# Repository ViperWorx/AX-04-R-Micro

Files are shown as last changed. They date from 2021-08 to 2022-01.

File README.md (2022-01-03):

<h1>AX-04-R Micro Core XY 3D Printer</h1>
<h3>Small, Compact, Rapid 3D Printer.</h3>

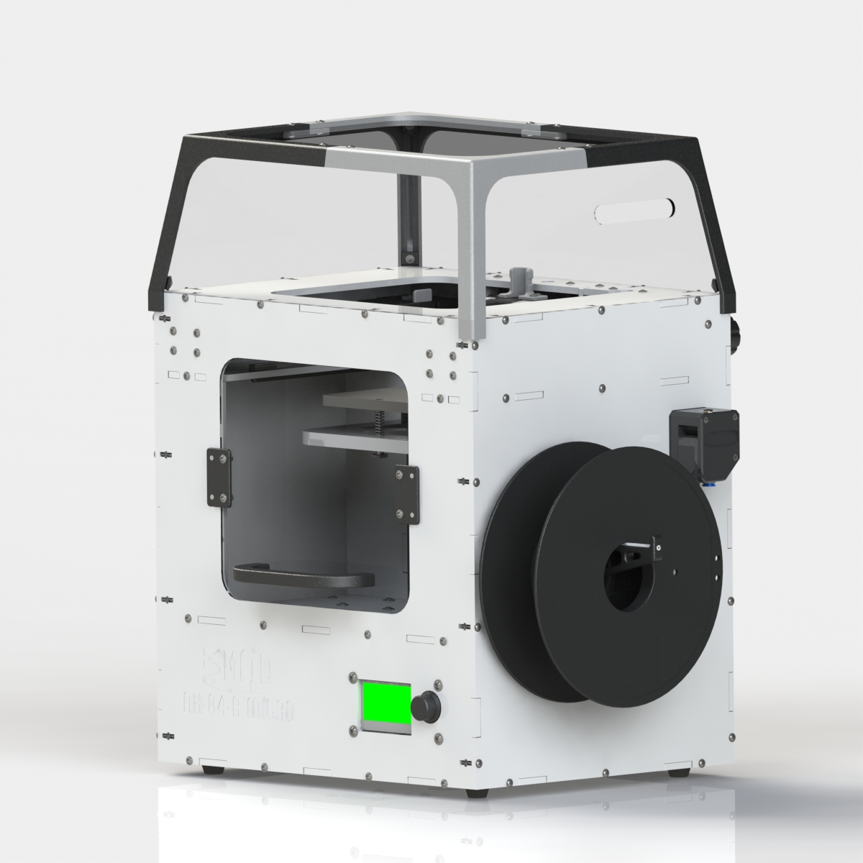
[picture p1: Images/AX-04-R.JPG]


The AX-04-R is a Acrylic bodied 3D Printer with a 120mm³ build volume.

<h4>Bill of Materials</h4>
You can find the Bill of material <a href="https://docs.google.com/spreadsheets/d/1N3T2BKN8lVm5PpJpeCxoxXIL51K7zTlElqo2wkVUTho/edit?usp=sharing">here</a>

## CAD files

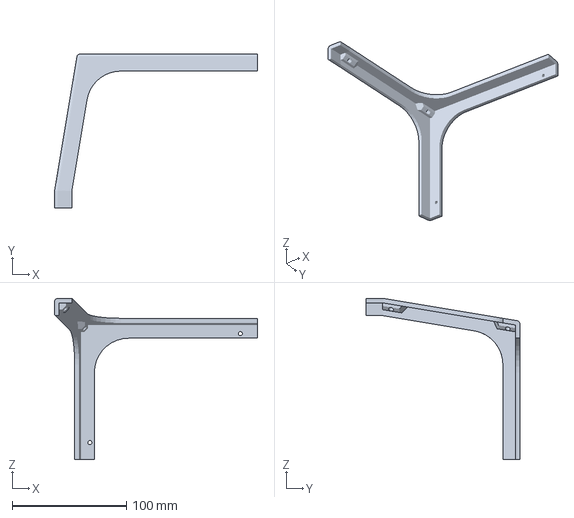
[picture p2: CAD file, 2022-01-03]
3MF/Top Hat Frame Quarter 2.3MF
178.0 x 135.0 x 141.5 mm

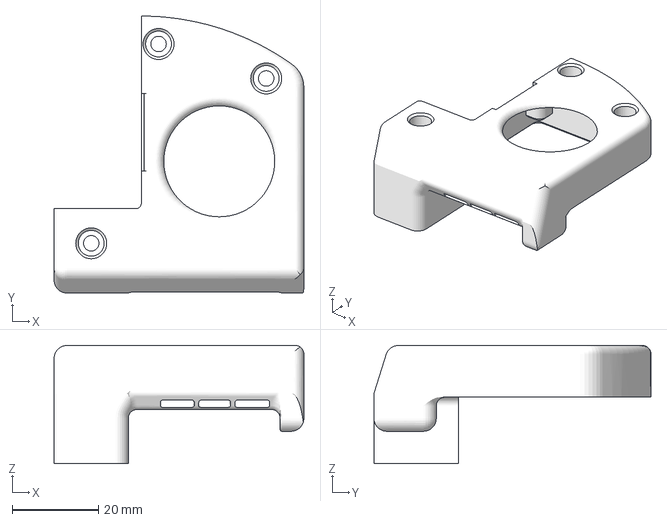
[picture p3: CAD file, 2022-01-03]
3MF/Layer Fan Mount Left.3MF
58.0 x 64.3 x 27.4 mm

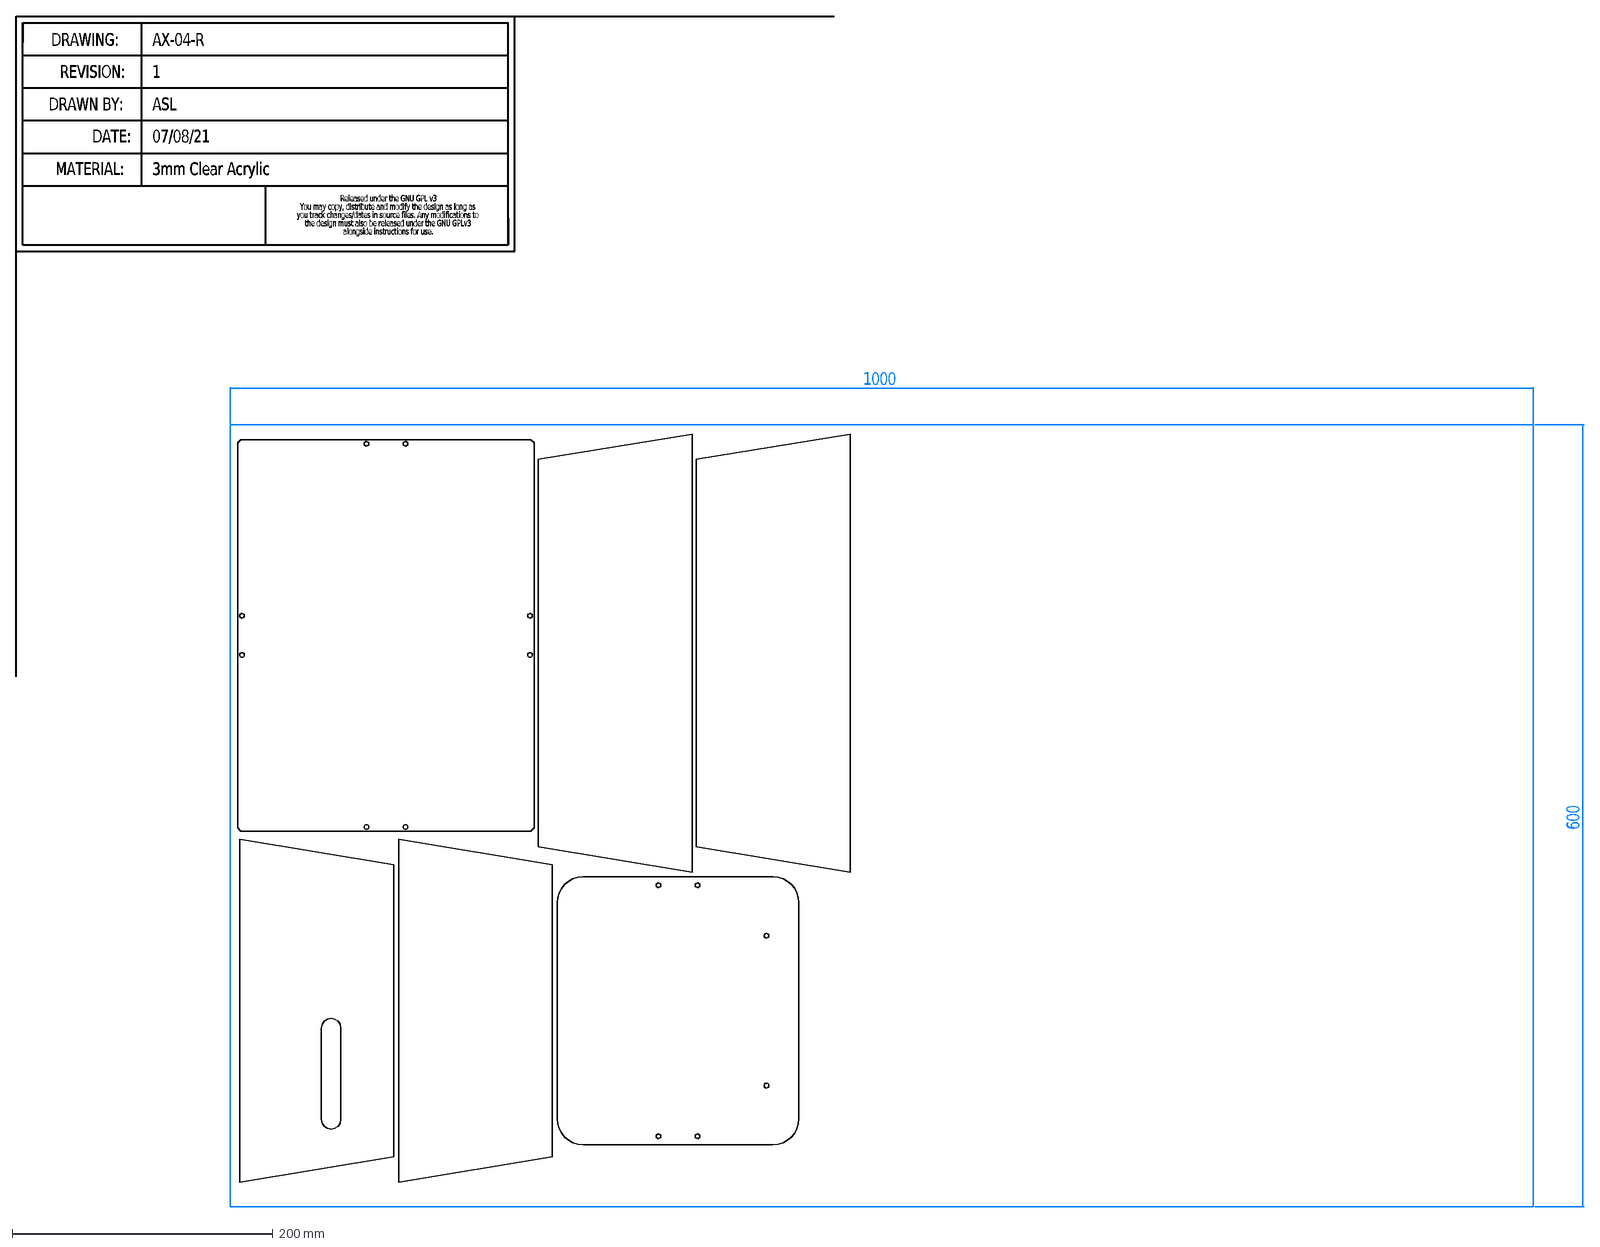
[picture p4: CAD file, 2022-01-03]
DXF/AX-04-R 3mm Clear Acrylic Laser Cut Parts.DXF
1000
600
Released under the GNU GPL v3
You may copy, distribute and modify the design as long as
you track changes/dates in source files. Any modifications to
the design must also be released under the GNU GPLv3
alongside instructions for use.
DRAWING:
REVISION:
DRAWN BY:
DATE:
MATERIAL:
AX-04-R
1
ASL
07/08/21
3mm Clear Acrylic

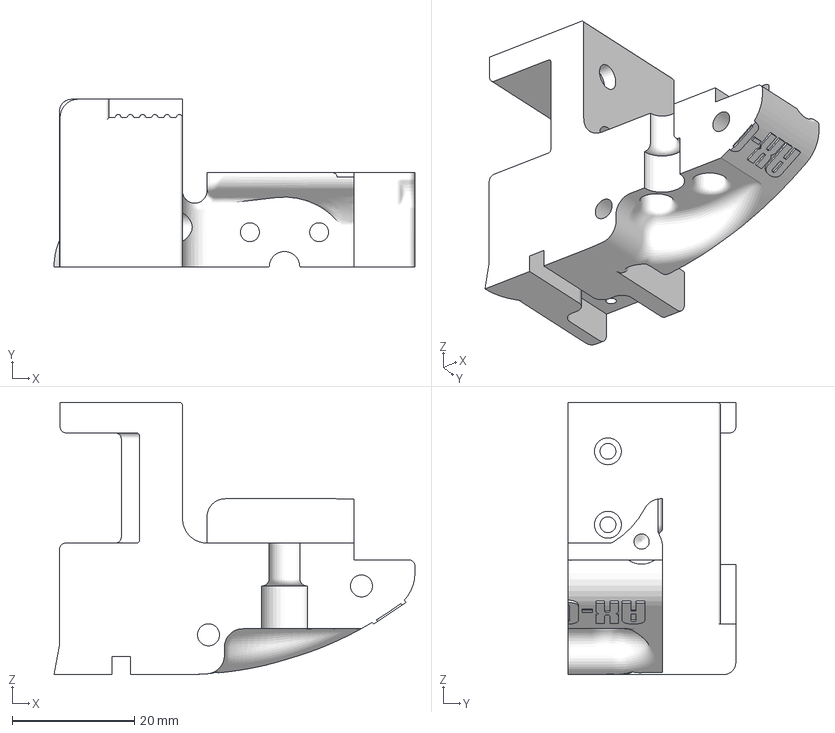
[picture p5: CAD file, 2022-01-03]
3MF/X Mount Left -Dragon Hotend.3MF
59.0 x 27.4 x 44.5 mm

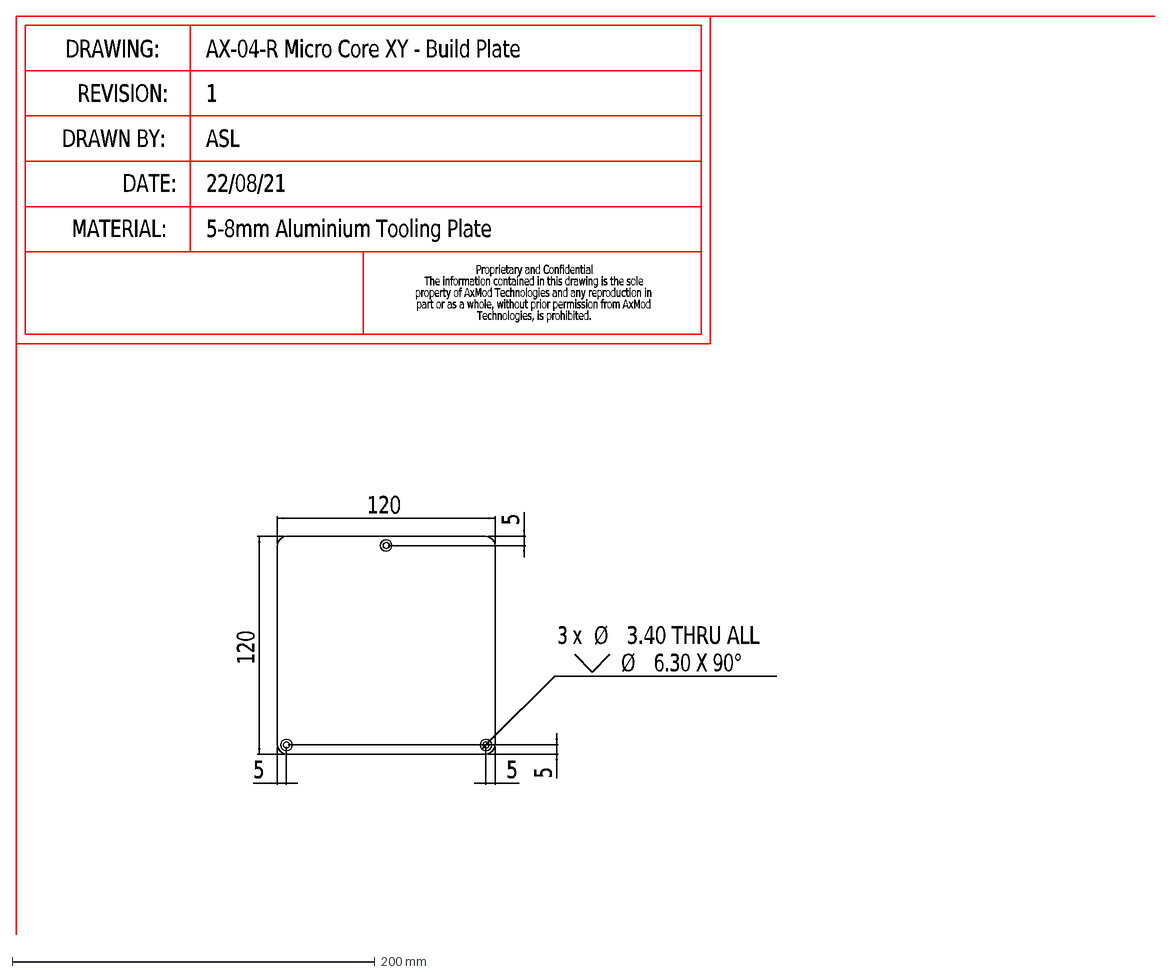
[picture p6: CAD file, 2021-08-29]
DXF/120x120 Print Bed.DXF
Proprietary and Confidential
The information contained in this drawing is the sole
property of AxMod Technologies and any reproduction in
part or as a whole, without prior permission from AxMod
Technologies, is prohibited.
DRAWING:
REVISION:
DRAWN BY:
DATE:
MATERIAL:
AX-04-R Micro Core XY - Build Plate
1
ASL
22/08/21
5-8mm Aluminium Tooling Plate
120
5
3 x
Ø
3.40 THRU ALL
6.30 X 90°

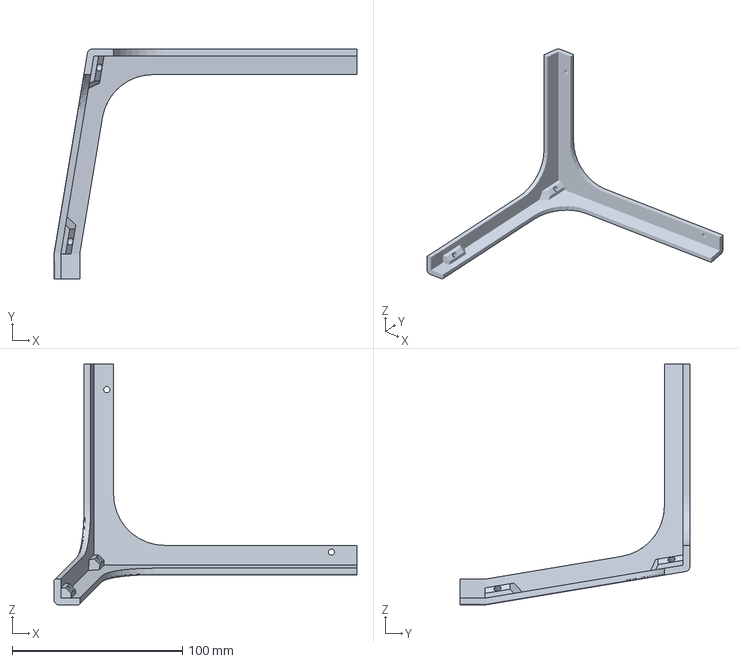
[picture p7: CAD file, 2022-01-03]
3MF/Top Hat Frame Quarter 4.3MF
178.0 x 135.0 x 141.5 mm

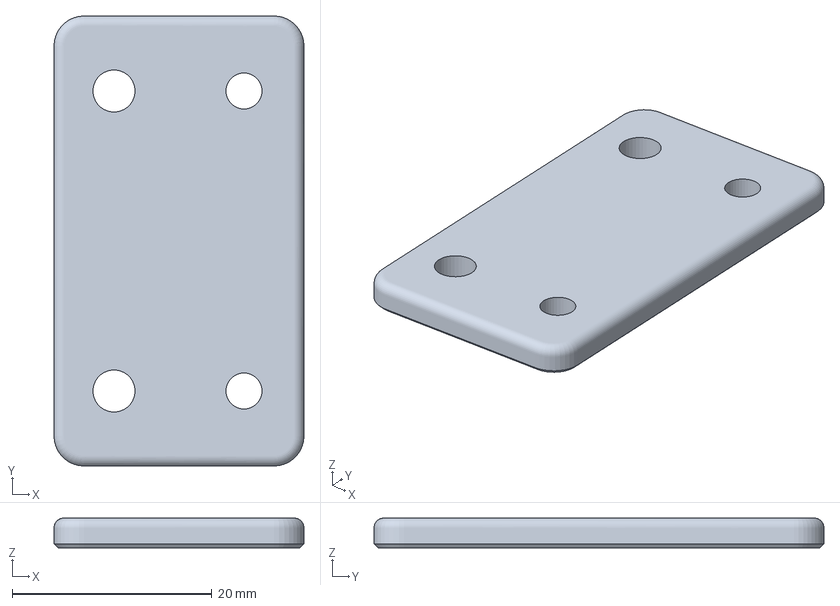
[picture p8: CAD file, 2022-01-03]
3MF/Front Window Magnet Plate.3MF
25.0 x 45.0 x 3.00 mm

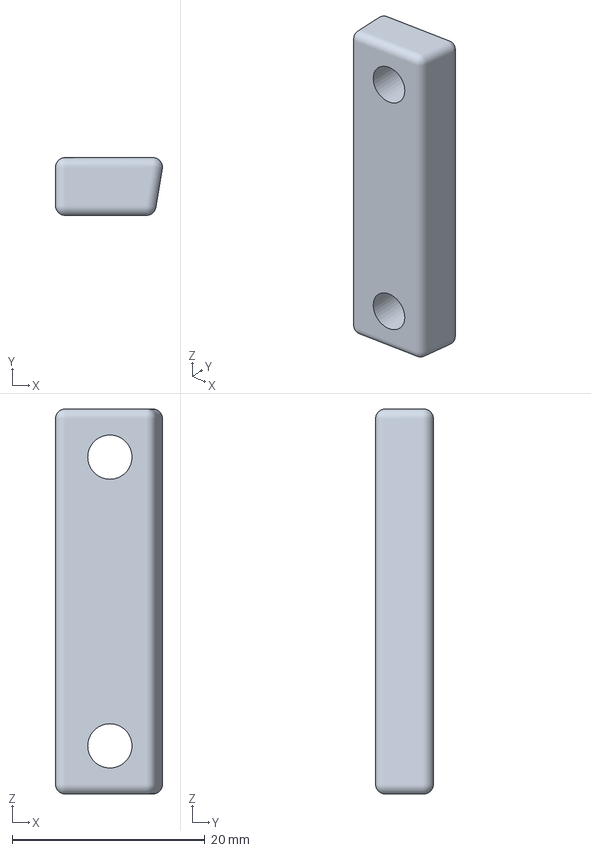
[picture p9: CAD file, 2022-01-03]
3MF/Top Hat Window Retainer Block Top.3MF
11.1 x 6.00 x 40.0 mm

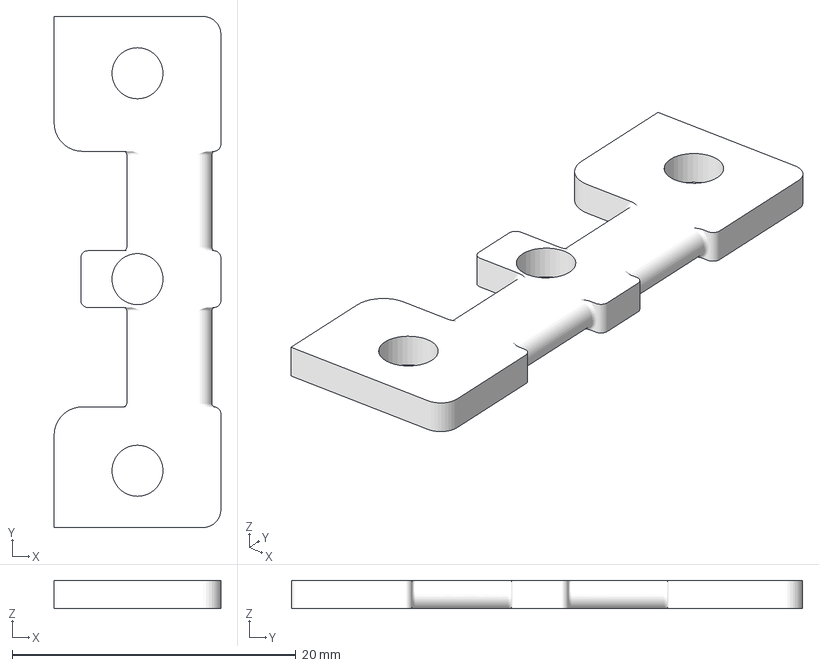
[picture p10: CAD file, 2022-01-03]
3MF/XY Belt Clamp.3MF
11.8 x 36.0 x 2.00 mm

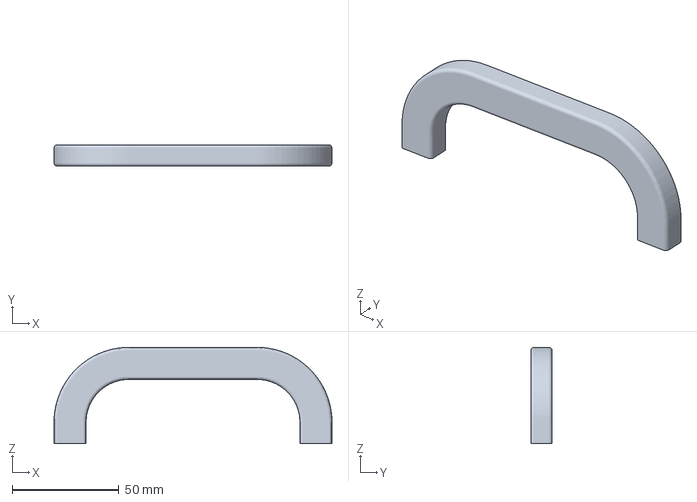
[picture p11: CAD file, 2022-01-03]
3MF/Front Window Handle.3MF
130.0 x 10.0 x 45.0 mm

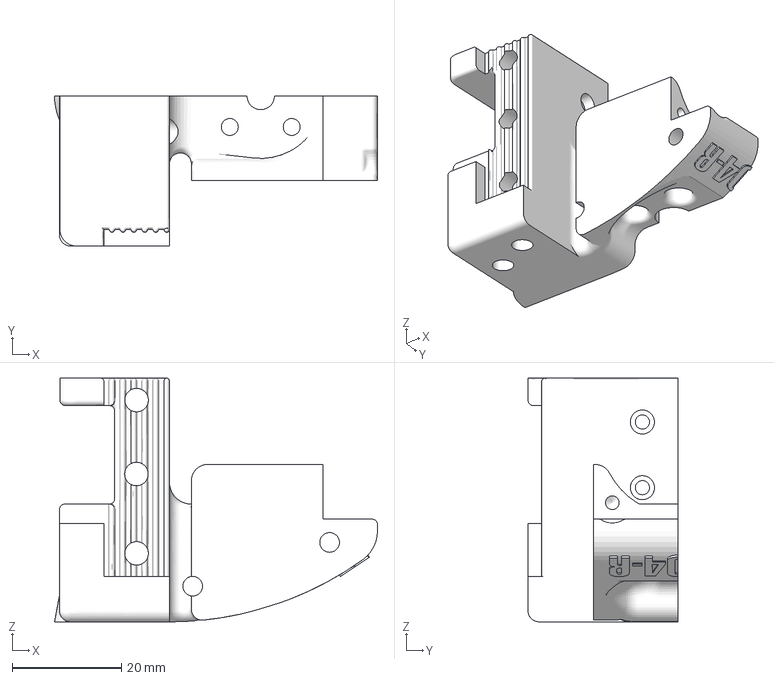
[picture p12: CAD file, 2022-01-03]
3MF/X Mount Right - Dragon Hotend.3MF
59.0 x 27.4 x 44.5 mm

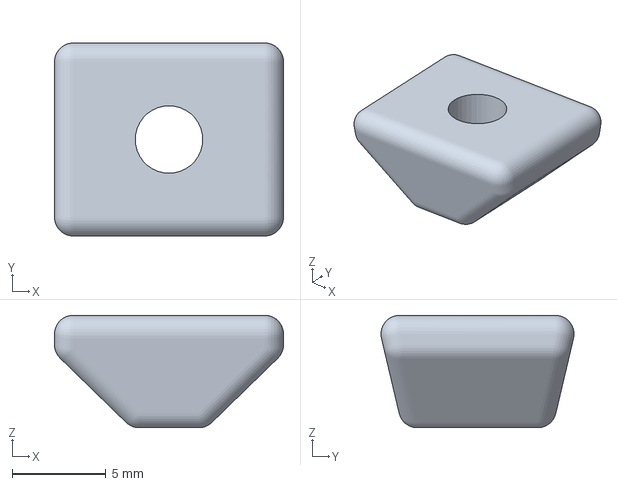
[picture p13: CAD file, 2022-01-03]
3MF/Top Hat Window Retainer Block Side.3MF
12.2 x 10.3 x 6.00 mm

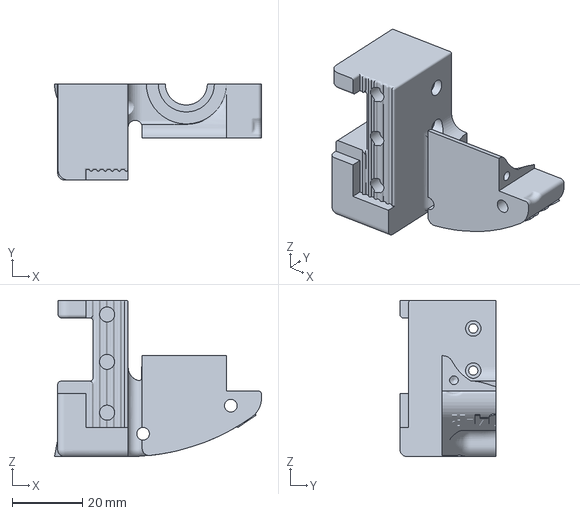
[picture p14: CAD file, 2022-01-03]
3MF/X Mount Right - Groovemount (E3D v6).3MF
59.0 x 27.4 x 44.5 mm

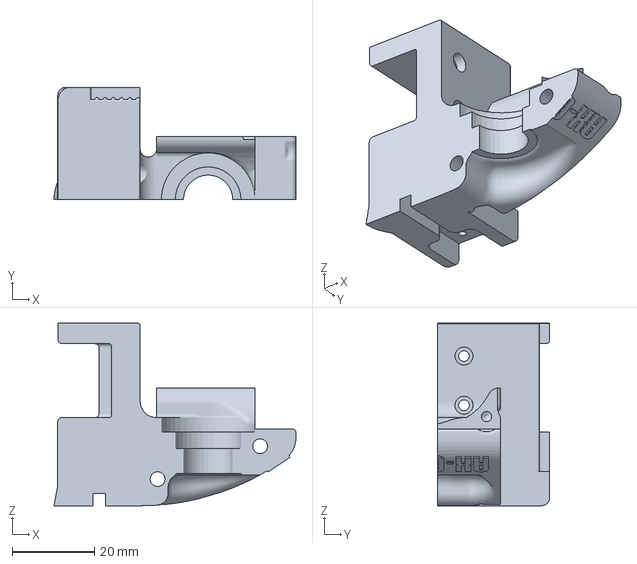
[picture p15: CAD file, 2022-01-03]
3MF/X Mount Left - Groovemount (E3D v6).3MF
59.0 x 27.4 x 44.5 mm

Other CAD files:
DXF/AX-04-R 5mm Acrylic Laser Cut Parts.DXF
3MF/Layer Fan Mount Right.3MF
3MF/Top Hat Frame Quarter 3.3MF
3MF/Top Hat Frame Quarter 1.3MF
3MF/Extruder Motor Shim.3MF
3MF/Foot Base.3MF
3MF/Idler Spacer.3MF
3MF/LED Mount Left-Right.3MF
3MF/LED Mount Top.3MF
3MF/M3 Stand off.3MF
3MF/Rail Retaining Bar - Half.3MF
3MF/Rail Retaining Bar.3MF
3MF/Spool Hanger.3MF
3MF/Tensioning Knob.3MF
3MF/X Alignment Tool.3MF
3MF/X Axis Umbilical Strain Relief Tool Head.3MF
3MF/X Axis Umbilical Strain Relief.3MF
3MF/X Endstop Interface.3MF
3MF/XY Idler Front Bottom Half.3MF
3MF/XY Idler Front Top Half.3MF
3MF/XY Motor Cap Left.3MF
3MF/XY Motor Cap Right.3MF
3MF/XY Motor Mount Left Bottom.3MF
3MF/XY Motor Mount Right Bottom.3MF
3MF/Y Carriage Left Bottom.3MF
3MF/Y Carriage Left Top.3MF
3MF/Y Carriage Right Bottom.3MF
3MF/Y Carriage Right Top.3MF
3MF/Y Endstop Mount.3MF
3MF/YZ Rail Alignment Tool.3MF
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

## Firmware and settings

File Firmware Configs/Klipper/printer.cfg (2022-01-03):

# This file pin mappings for the BIGTREETECH SKR mini
# E3 v2.0 for the AX-04-R Micro. 

#To use this config, the firmware should be compiled for the
# STM32F103 with a "28KiB bootloader" and USB communication. Also,
# select "Enable extra low-level configuration options" and configure
# "GPIO pins to set at micro-controller startup" to "!PA14".

[stepper_x]
step_pin: PB10
dir_pin: PB2
enable_pin: !PB11
microsteps: 32
rotation_distance: 40
endstop_pin: ^PC0
position_endstop: -14
position_min: -14
position_max: 120
homing_speed: 80

[tmc2209 stepper_x]
uart_pin: PC11
tx_pin: PC10
uart_address: 0
run_current: 0.58
hold_current: 0.4
stealthchop_threshold: 999999

[endstop_phase stepper_x]

[stepper_y]
step_pin: PB13
dir_pin: PB12
enable_pin: !PB14
microsteps: 32
rotation_distance: 40
endstop_pin: ^PC1
position_endstop: 122
position_min: 0
position_max: 122
homing_speed: 80

[tmc2209 stepper_y]
uart_pin: PC11
tx_pin: PC10
uart_address: 2
run_current: 0.58
hold_current: 0.5
stealthchop_threshold: 999999

[endstop_phase stepper_y]

[stepper_z]
step_pin: PB0
dir_pin: !PC5
enable_pin: !PB1
microsteps: 32
rotation_distance: 40
endstop_pin: ^PC2
position_endstop: 0.0
position_max: 120
gear_ratio: 80:20
homing_speed: 30

[tmc2209 stepper_z]
uart_pin: PC11
tx_pin: PC10
uart_address: 1
run_current: 0.58
hold_current: 0.5
stealthchop_threshold: 999999

[endstop_phase stepper_z]

[extruder]
step_pin: PB3
dir_pin: !PB4
enable_pin: !PD2
microsteps: 32
rotation_distance: 23.056
gear_ratio: 50:17
nozzle_diameter: 0.400
filament_diameter: 1.750
heater_pin: PC8
sensor_type: ATC Semitec 104GT-2
sensor_pin: PA0
control: pid
pid_Kp: 21.527
pid_Ki: 1.063
pid_Kd: 108.982
max_temp: 300
max_extrude_cross_section = 10
max_extrude_only_distance = 550

[tmc2209 extruder]
uart_pin: PC11
tx_pin: PC10
uart_address: 3
run_current: 0.680
hold_current: 0.600
stealthchop_threshold: 999999

[heater_bed]
heater_pin: PC9
sensor_type: NTC 100K beta 3950
sensor_pin: PC3
control: pid
pid_Kp: 54.027
pid_Ki: 0.770
pid_Kd: 948.182
min_temp: 0
max_temp: 130

[heater_fan hotend]
pin: PC7
heater_temp: 55.0
fan_speed: 1.0
heater: extruder

[fan]
pin: PC6
kick_start_time: 0.100
shutdown_speed: 0

[mcu]
serial: /dev/serial/by-id/usb-Klipper_stm32f103xe_32FFD9055359393542790743-if00

[printer]
kinematics: corexy
max_velocity: 300
max_accel: 3000
max_z_velocity: 150
max_z_accel: 3000
square_corner_velocity: 2.0

[virtual_sdcard]
path: ~/gcode_files/

[static_digital_output usb_pullup_enable]
pins: !PA14

[output_pin ps_on]
pin: PC13
value: 0
shutdown_value: 0

[display]
lcd_type: uc1701
cs_pin: PB8
a0_pin: PB15
rst_pin: PB9
encoder_pins: ^PA9,^PA10
click_pin: ^!PB5
contrast: 63
spi_software_sclk_pin: PA5
spi_software_mosi_pin: PA7
spi_software_miso_pin: PA6
menu_timeout: 30

[neopixel lcd]
pin: PA8
chain_count: 3
color_order: RGB
initial_RED: 0.1
initial_GREEN: 0.1
initial_BLUE: 0.1

[bed_screws]
screw1: 60,15
screw2: 105,105
screw3: 15,105

[include fluidd-ax-04-r.cfg]

[include macros-ax-04-r.cfg]

[include menu-ax-04-r.cfg]

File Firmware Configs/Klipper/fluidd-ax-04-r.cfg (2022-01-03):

[display_status]

[pause_resume]

[gcode_macro PAUSE]
description: Pause the actual running print
rename_existing: PAUSE_BASE
# change this if you need more or less extrusion
variable_extrude: 1.0
gcode:
  ##### read E from pause macro #####
  {% set E = printer["gcode_macro PAUSE"].extrude|float %}
  ##### set park positon for x and y #####
  # default is your max posion from your printer.cfg
  {% set x_park = printer.toolhead.axis_minimum.x|float - 5.0 %}
  {% set y_park = printer.toolhead.axis_minimum.y|float - 5.0 %}
  ##### calculate save lift position #####
  {% set max_z = printer.toolhead.axis_maximum.z|float %}
  {% set act_z = printer.toolhead.position.z|float %}
  {% if act_z < (max_z - 2.0) %}
      {% set z_safe = 2.0 %}
  {% else %}
      {% set z_safe = max_z - act_z %}
  {% endif %}
  ##### end of definitions #####
  PAUSE_BASE
  G91
  {% if printer.extruder.can_extrude|lower == 'true' %}
    G1 E-{E} F2100
  {% else %}
    {action_respond_info("Extruder not hot enough")}
  {% endif %}
  {% if "xyz" in printer.toolhead.homed_axes %}
    G1 Z{z_safe} F900
    G90
    G1 X{x_park} Y{y_park} F6000
  {% else %}
    {action_respond_info("Printer not homed")}
  {% endif %} 
  
[gcode_macro RESUME]
description: Resume the actual running print
rename_existing: RESUME_BASE
gcode:
  ##### read E from pause macro #####
  {% set E = printer["gcode_macro PAUSE"].extrude|float %}
  #### get VELOCITY parameter if specified ####
  {% if 'VELOCITY' in params|upper %}
    {% set get_params = ('VELOCITY=' + params.VELOCITY)  %}
  {%else %}
    {% set get_params = "" %}
  {% endif %}
  ##### end of definitions #####
  {% if printer.extruder.can_extrude|lower == 'true' %}
    G91
    G1 E{E} F2100
  {% else %}
    {action_respond_info("Extruder not hot enough")}
  {% endif %}  
  RESUME_BASE {get_params}

[gcode_macro CANCEL_PRINT]
description: Cancel the actual running print
rename_existing: CANCEL_PRINT_BASE
gcode:
  G91
  G1 E-1 F300
  G1 E-5 F4800
  G1 Z+5 F420
  G90
  M106 S0
  TURN_OFF_HEATERS
  G28X
  G28Y
  M84
  CANCEL_PRINT_BASE
  SET_LED LED=lcd RED=1 GREEN=1 BLUE=1

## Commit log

2021-08-29 Update Gitignore, remove Incorrect BOM
    [AX-04-R Micro Core XY Buying list.xlsx]
2021-08-29 Add X Mount for Groove mounting hot ends like the E3D v6
    [X Mount Left - Groovemount (E3D v6).3MF, X Mount Right - Groovemount (E3D v6).3MF]
2021-08-29 Rename Original X Mount files for clarity
    [X Mount Left -Dragon Hotend.3MF, X Mount Right - Dragon Hotend.3MF]
2021-09-01 Update 3D Print files
    [LED Mount Left.3MF, LED Mount Right.3MF, Motor Tensioner.3MF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]
2021-09-08 Remove Excel Files
    [AX-04-R Micro Core XY - Bill of Materials (1).xlsx]
2021-09-08 Change IEC Inlet for Fused version
    [AX-04-R Laser Cut Parts.DXF]
2021-09-08 Add 1.38mm to Z Belt clamp to Straighten belt path
    [Z Axis Belt Clamp - Bottom.3MF, Z Axis Belt Clamp - Mid.3MF, Z Axis Belt Clamp - Top.3MF]
2021-09-09 Reduce M3x16 FBH Bolts/Nuts by 8
    Wire covering vanity panels are not structural so only 2 sets of fixings needed. Also makes the panels easier to install and remove
    [AX-04-R Laser Cut Parts.DXF]
2021-09-11 Update CAD files due to error
2021-09-11 Add Klipper Firmwar Configs & Start/End GCode Scripts
    [fluidd-ax-04-r.cfg, macros-ax-04-r.cfg, menu-ax-04-r.cfg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]
2021-09-11 Upload correct version of printer.cfg
    [printer.cfg]
2021-09-11 XY Belt Clamp - Add Extra Spur to allow for easier belt alignment
    [XY Belt Clamp.3MF]
2021-09-19 Add Top Hat and Front Window to Enclose printer
    [AX-04-R 3mm Clear Acrylic Laser Cut Parts.DXF, AX-04-R 5mm Acrylic Laser Cut Parts.DXF, AX-04-R Laser Cut Parts.DXF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]
2021-09-19 Correct location of slot for bowden tube in top hat
    [AX-04-R 3mm Clear Acrylic Laser Cut Parts.DXF]
2021-09-19 Clear duplicate files
    [Motor Tensioner.3MF, X Mount Left.3MF, X Mount Right.3MF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]
2021-09-19 Further Clearing of duplicate files
    [LED Mount Centre.3MF, LED Mount Left.3MF, LED Mount Right.3MF]
2021-10-21 Extend Ducts by 2mm
    Improvement on cooling. Fans were blowing hot air
    [Layer Fan Mount Left.3MF, Layer Fan Mount Right.3MF]
2021-10-23 Add Clearance from Heater Block
    Air output too close to heater block. Ducts were melting
    [Layer Fan Mount Left.3MF, Layer Fan Mount Right.3MF]
2021-10-23 Add clearance for belt clamp/remove inconsistencies from each side
    Clearance for belt clamp added to top of belt clamp area. Belt clamp area -one corner filleted on one side and one not, fillet removed
    [X Mount Left - Groovemount (E3D v6).3MF, X Mount Left -Dragon Hotend.3MF, X Mount Right - Dragon Hotend.3MF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]
2021-10-23 Remove added 2mm length to fan ducts
    Ducts were dragging on print causing inconsistencies in first layer
    [Layer Fan Mount Left.3MF, Layer Fan Mount Right.3MF]
2021-10-23 Correct fitment issue
    Rear fan duct part interfering with X tool head mount
    [Layer Fan Mount Left.3MF, Layer Fan Mount Right.3MF]
2022-01-03 Add Klipper Firmware Configs & Start/End GCode Scripts
    [fluidd-ax-04-r.cfg, macros-ax-04-r.cfg, menu-ax-04-r.cfg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]
